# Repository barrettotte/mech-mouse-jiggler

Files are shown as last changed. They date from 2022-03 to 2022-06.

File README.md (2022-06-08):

# mech-mouse-jiggler

A very impractical and stupid mouse jiggler using a crank mechanism, 12V DC motor, and a PWM circuit.

## Purpose

I wanted a basic project with some gears, a mechanical movement, and a DC motor. 
So this was the simplest thing I could think of; Move a mouse back and forth.

The mechanical movement and gears gave me more experience with components/joints in Fusion 360.
I also took the opportunity to learn KiCad and design a PCB for my basic PWM circuit.

## Finished Project

Definitely not perfect and I kept finding flaws. But, it was good enough for the project scope I made.





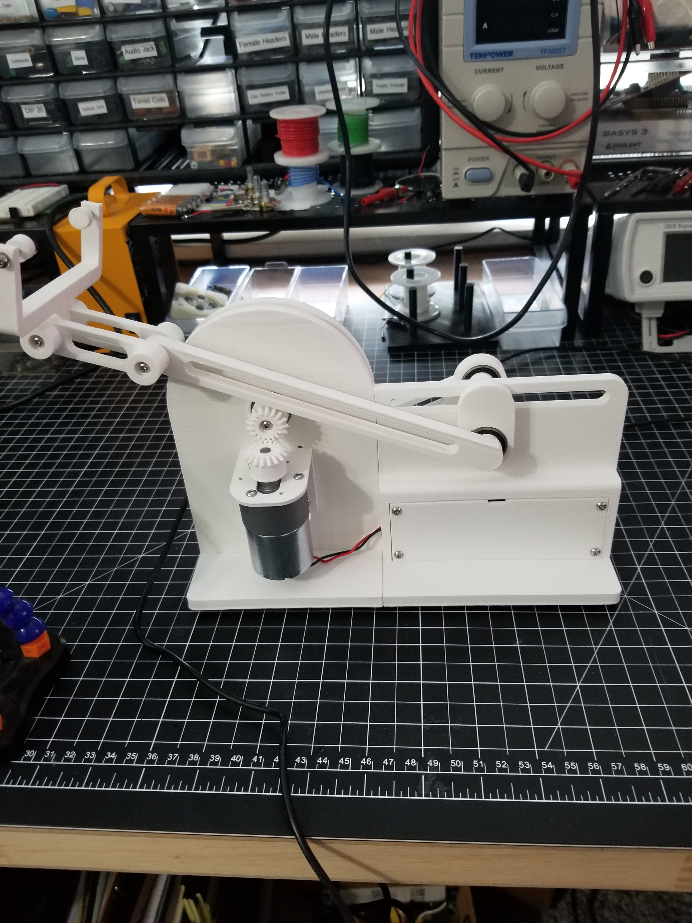
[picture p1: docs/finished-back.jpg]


https://user-images.githubusercontent.com/15623775/172682833-343187b7-290f-4d06-a3b5-5a9f5e372b6b.mp4

https://user-images.githubusercontent.com/15623775/172682868-b304a3e7-49c9-4841-98fb-ab1815b85bfa.mp4

## PWM Circuit

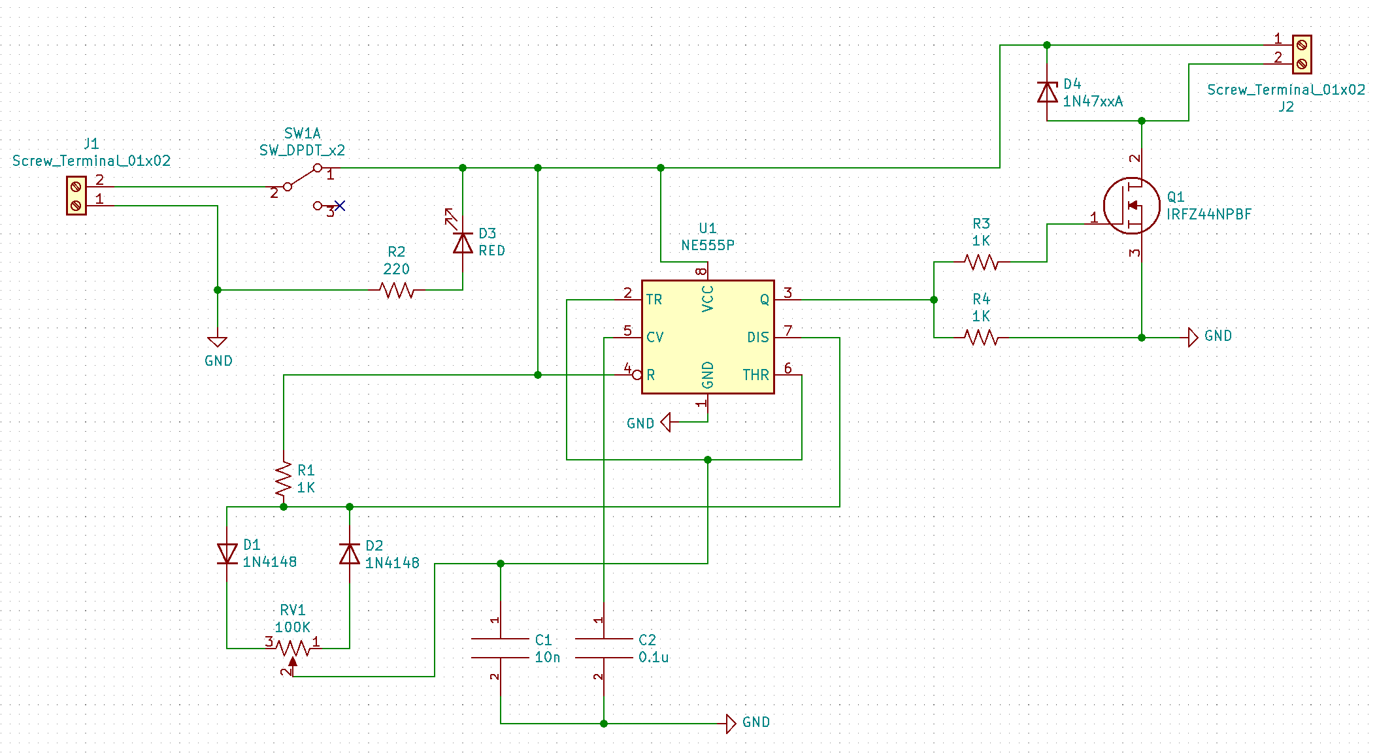
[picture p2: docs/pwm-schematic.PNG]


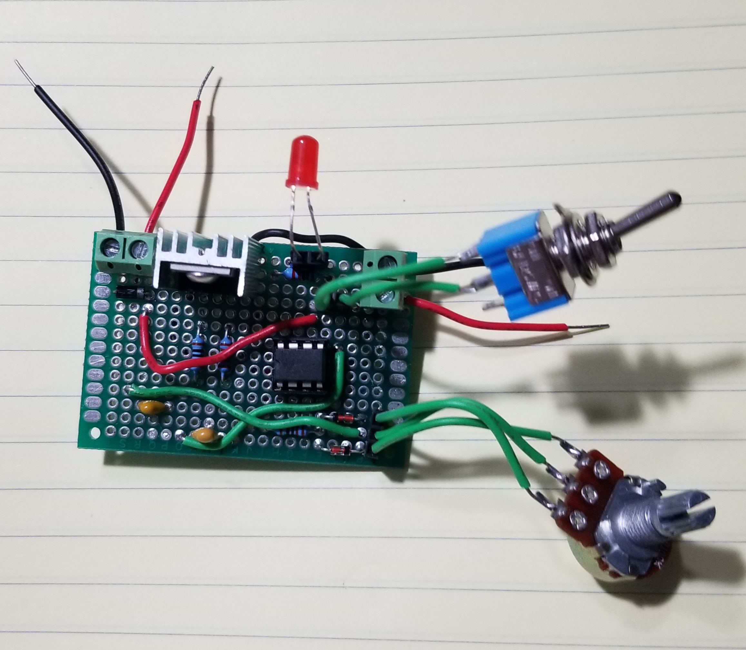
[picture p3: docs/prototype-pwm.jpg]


Crank Test 1 (https://youtube.com/shorts/KTGvGtsnRqs)

Crank Test 2 (https://youtube.com/shorts/8-THsEUhmM4)

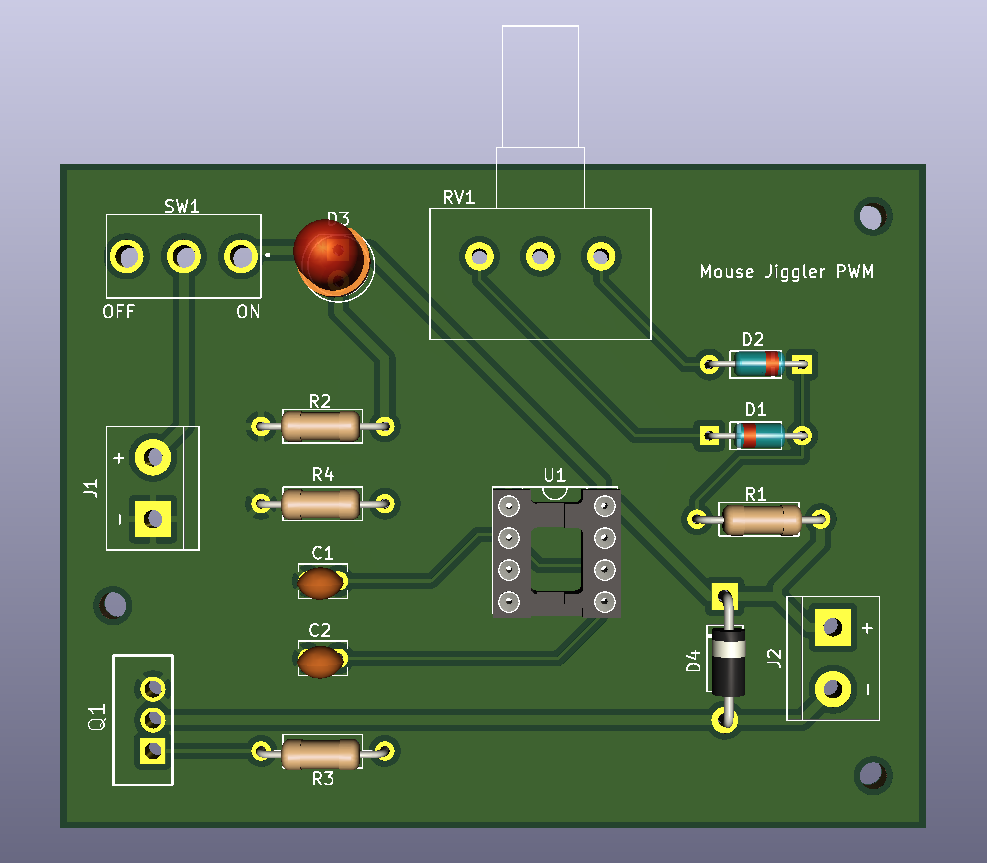
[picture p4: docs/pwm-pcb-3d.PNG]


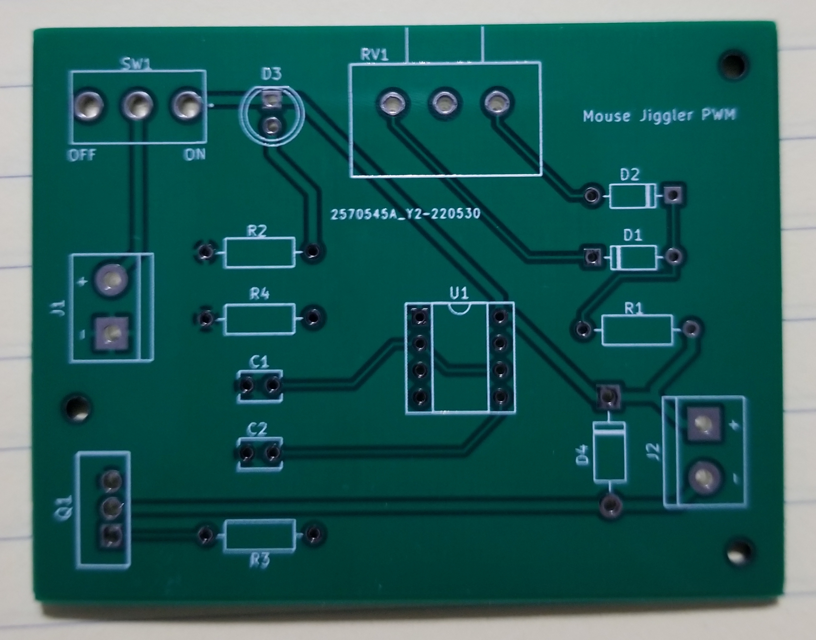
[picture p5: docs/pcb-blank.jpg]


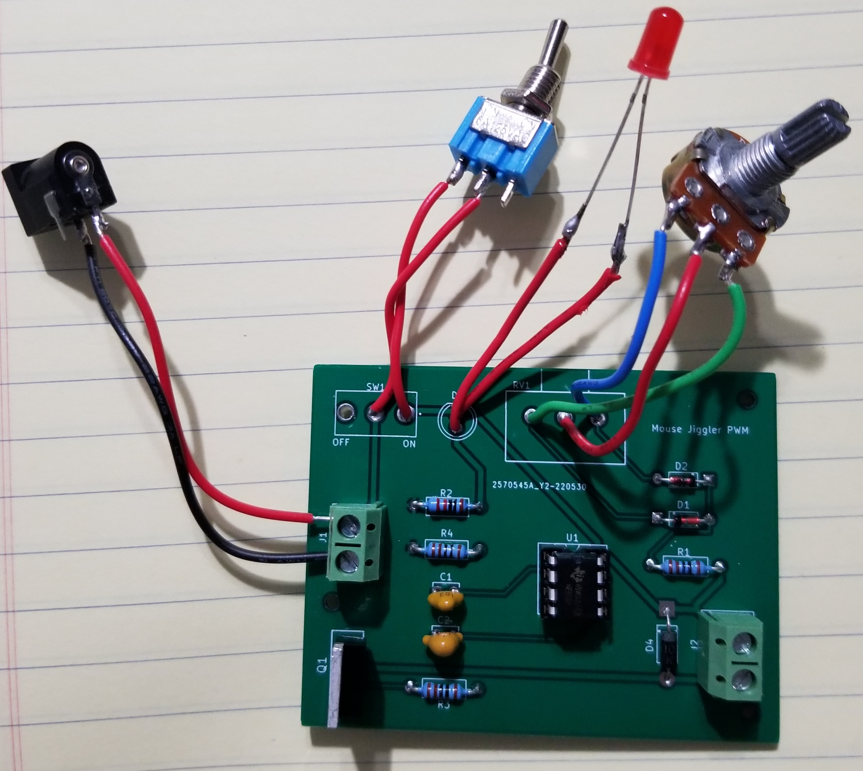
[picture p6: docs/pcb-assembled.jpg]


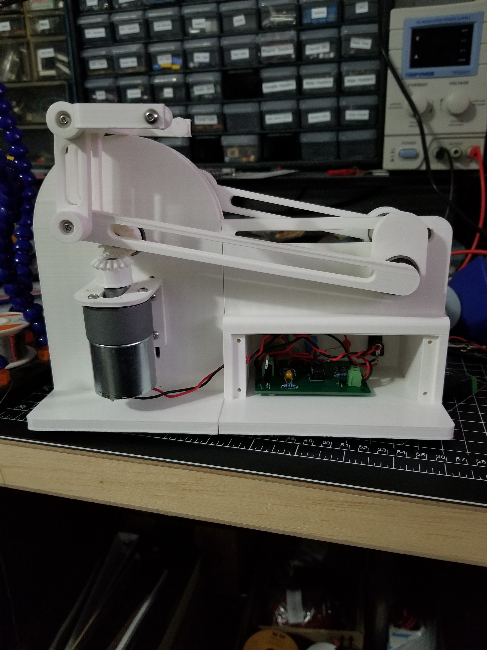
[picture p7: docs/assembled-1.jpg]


## References

- [507 Movements #92](http://507movements.com/mm_092.html)
- [507 Movements #114](http://507movements.com/mm_114.html)
- [KHK Gear Reference](https://khkgears.net/new/gear_knowledge/gear_technical_reference/involute_gear_profile.html)
- [555 Timer PWM circuit](http://www.555-timer-circuits.com/motor-pwm.html)

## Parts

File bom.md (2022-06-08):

# Bill of Materials

## Electronics

| Component Refs | Name | Quantity | Digkey | Link |
| --- | --- | --- | --- | ---- |
| C1 | 10nF Ceramic Capacitor | 1 | 399-5094-ND | https://www.digikey.com/en/products/detail/kemet/C330C102JHR5TA/1465599 |
| C2 | 0.1µF Ceramic Capacitor  | 1 | 399-4329-ND | https://www.digikey.com/en/products/detail/kemet/C322C104K5R5TA/818105 |
| D1,D2 | 1N4148 Diode | 2 | 4167-1N4148-ND | https://www.digikey.com/en/products/detail/diotec-semiconductor/1N4148/16141550 |
| D3 | 5mm Red LED | 1 | 2460-L513SRD-C-ND | https://www.digikey.com/en/products/detail/american-opto-plus-led/L513SRD-C/13556881 |
| D4 | 1N4007T Diode | 1 | 1N4007DICT-ND | https://www.digikey.com/en/products/detail/diodes-incorporated/1N4007-T/607 |
| J1,J2 | 1x2 Terminal Block | 2 | 732-691253910002-ND | https://www.digikey.com/en/products/detail/w%C3%BCrth-elektronik/691253910002/11477907 |
| R1,R3,R4 | 1KΩ Resistor | 3 | CFR25SJT-52-1K-ND | https://www.digikey.com/en/products/detail/yageo/CFR25SJT-52-1K/9098875 |
| R2 | 220Ω Resistor | 1 | CFR25SJT-52-220R-ND  | https://www.digikey.com/en/products/detail/yageo/CFR25SJT-52-220R/9098891 |
| RV1 | 100KΩ Potentiometer | 1 | PDB181-K220K-104B-ND | https://www.digikey.com/en/products/detail/bourns-inc/PDB181-K220K-104B/3780702 | 
| SW1 | Toggle Switch | 1 | 2057-SW-T3-2B-A-A3-S1-ND | https://www.digikey.com/en/products/detail/adam-tech/SW-T3-2B-A-A3-S1/15284416 |
| Q1 | IRFZ44N MOSFET | 1 | IRFZ44NLPBF-ND | https://www.digikey.com/en/products/detail/infineon-technologies/IRFZ44NLPBF/811989 |
| U1 | NE555P IC | 1 | 296-NE555P-ND | https://www.digikey.com/en/products/detail/texas-instruments/NE555P/277057 |
| - | 8 pin DIP socket | 1 | 1175-1486-ND | https://www.digikey.com/en/products/detail/cnc-tech/245-08-1-03/3441579 |
| - | Male barrel jack | 1 | CP-102A-ND | https://www.digikey.com/en/products/detail/cui-devices/PJ-102A/275425 |

## Mechanical

| Name | Quantity | McMaster-Carr | Link |
| --- | --- | --- | ---- |
| 12V DC 550RPM Gear Motor 37mm Shaft | 1 | - | https://www.amazon.com/gp/product/B072R5G5GR |
| 608 Bearing, 8mm shaft | 4 | 5972K91 | https://www.mcmaster.com/5972K91 |
| M3 Hex Button Cap 16mm | 3 | 92095A184 | https://www.mcmaster.com/92095A184 |
| M3 Hex Button Cap 12mm | 11 | 92095A183 | https://www.mcmaster.com/92095A183 |
| M3 Hex Button Cap 6mm | 5 | 92095A179 | https://www.mcmaster.com/92095A179 |
| M3 nut | 4 | 90592A085 | https://www.mcmaster.com/90592A085 |
| Rubber feet 12mm | 6 | - | https://www.amazon.com/gp/product/B07PXNTT7K |

## 3D Printed

Creality Ender-3 Pro - 0.4mm nozzle, 0.2mm layer height, 20% infill

| Name | Quantity | Model |
| --- | --- | ----- |
| Arm | 1 | [cad/arm.3mf](cad/arm.3mf) |
| Arm connector | 2 | [cad/arm_connector.3mf](cad/arm_connector.3mf) |
| Base | 1 | [cad/base.3mf](cad/base.3mf) |
| Base electonics | 1 | [cad/base_electronics.3mf](cad/base_electronics.3mf) |
| Bearing cap | 3 | [cad/bearing_cap.3mf](cad/bearing_cap.3mf) |
| Bevel gear motor  | 1 | [cad/bevel_gear_motor.3mf](cad/bevel_gear_motor.3mf) |
| Bevel gear wheel  | 1 | [cad/bevel_gear_wheel.3mf](cad/bevel_gear_wheel.3mf) |
| Coupler | 1 | [cad/coupler.3mf](cad/coupler.3mf) |
| Electronics Cover | 1 | [cad/electronics_cover.3mf](cad/electronics_cover.3mf) |
| Load arm | 1 | [cad/load_arm.3mf](cad/load_arm.3mf) |
| Motor mount | 1 | [cad/motor_mount.3mf](cad/motor_mount.3mf) |
| Mouse clamp | 1 | [cad/mouse_clamp.3mf](cad/mouse_clamp.3mf) |
| Mouse clamp cap | 2 | [cad/mouse_clamp_cap.3mf](cad/mouse_clamp_cap.3mf) |
| Wheel spacer | 3 | [cad/wheel_spacer.3mf](cad/wheel_spacer.3mf) |
| Wheel | 1 | [cad/wheel.3mf](cad/wheel.3mf) |

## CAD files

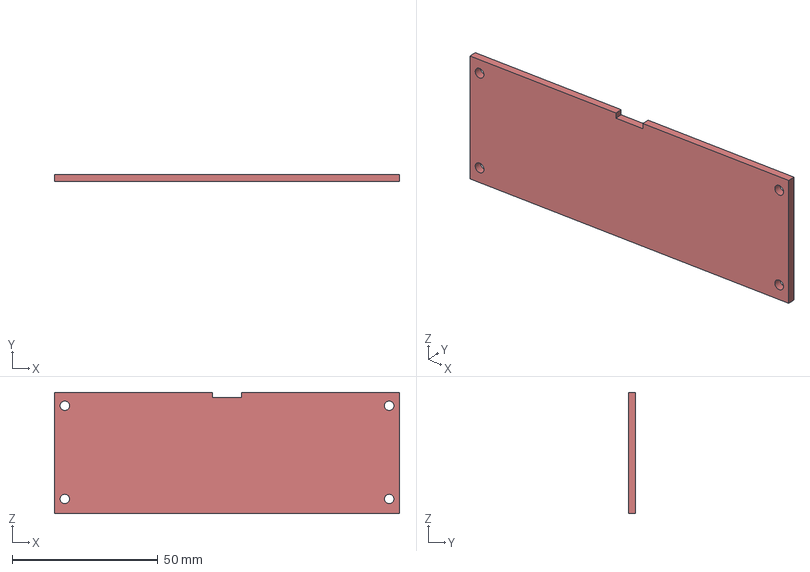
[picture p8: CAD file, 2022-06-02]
cad/electronics-cover.3mf
118.5 x 2.50 x 41.5 mm

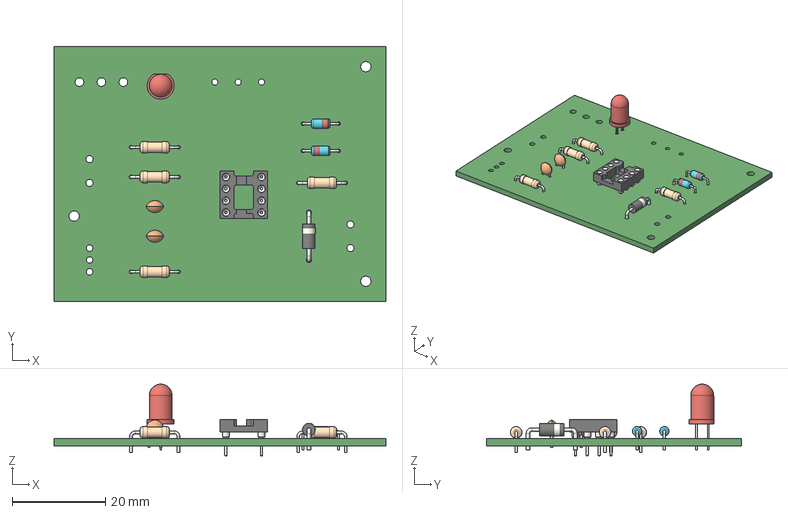
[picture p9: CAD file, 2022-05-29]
eda/mouse-jiggler-pwm.step
71.1 x 54.6 x 15.4 mm

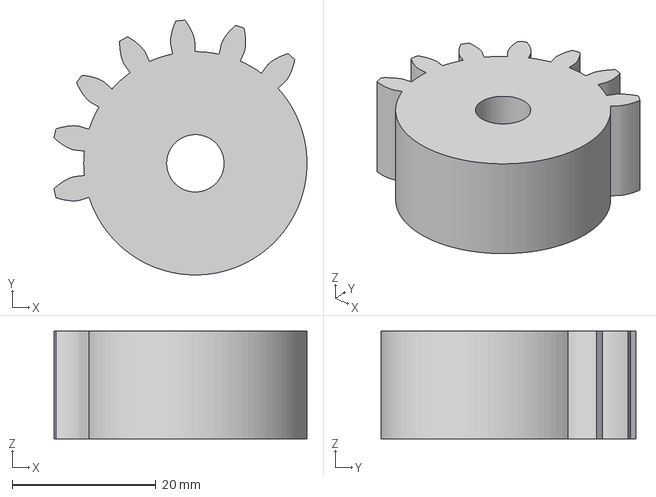
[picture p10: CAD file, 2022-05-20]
test/movement-114/mutilated-spur-gear-15-7.3mf
35.2 x 35.5 x 15.0 mm

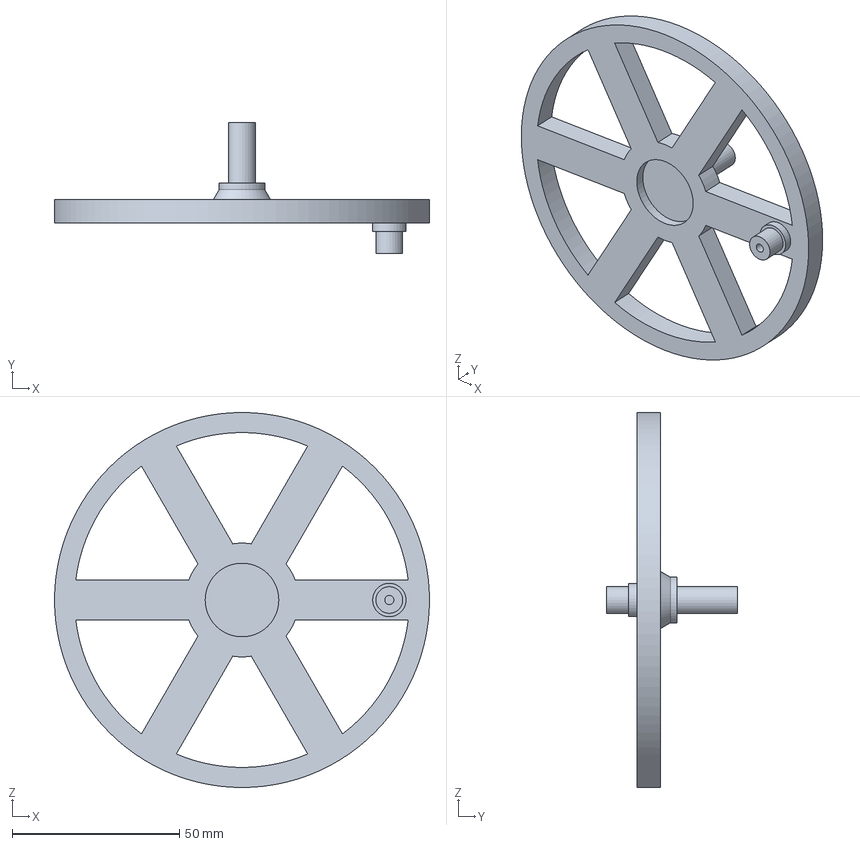
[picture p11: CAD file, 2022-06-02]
cad/wheel.3mf
112.0 x 39.0 x 112.0 mm

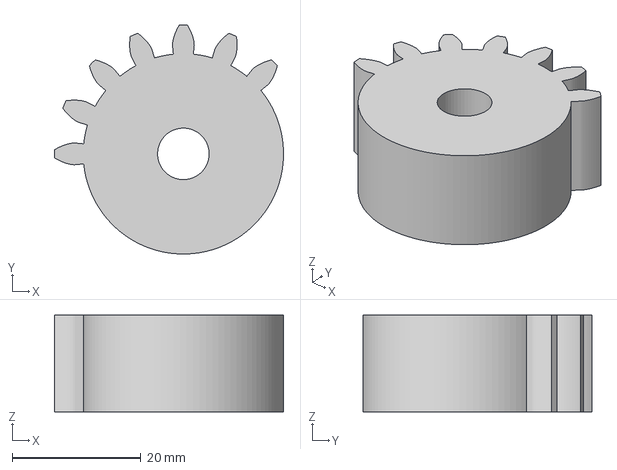
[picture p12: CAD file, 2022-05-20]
test/movement-114/mutilated-spur-gear-16-7.3mf
35.5 x 35.5 x 15.0 mm

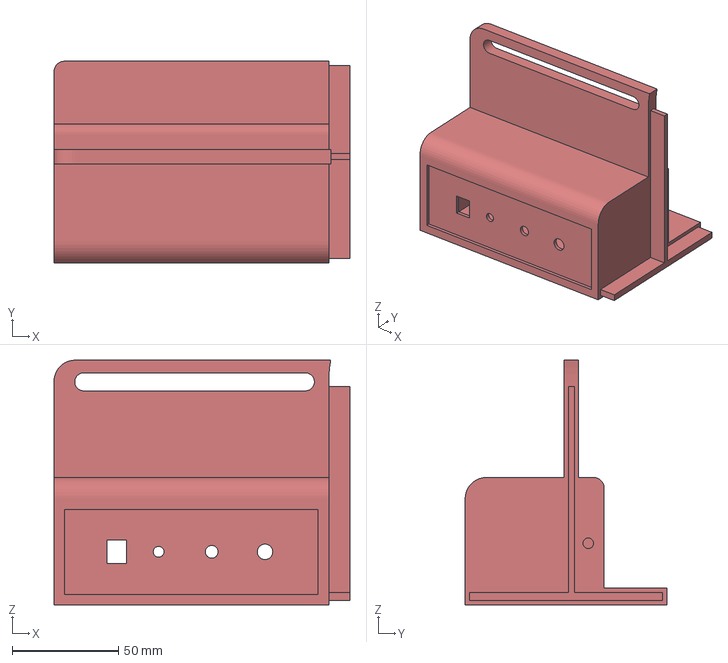
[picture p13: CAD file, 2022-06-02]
cad/base-electronics.3mf
139.4 x 95.0 x 115.2 mm

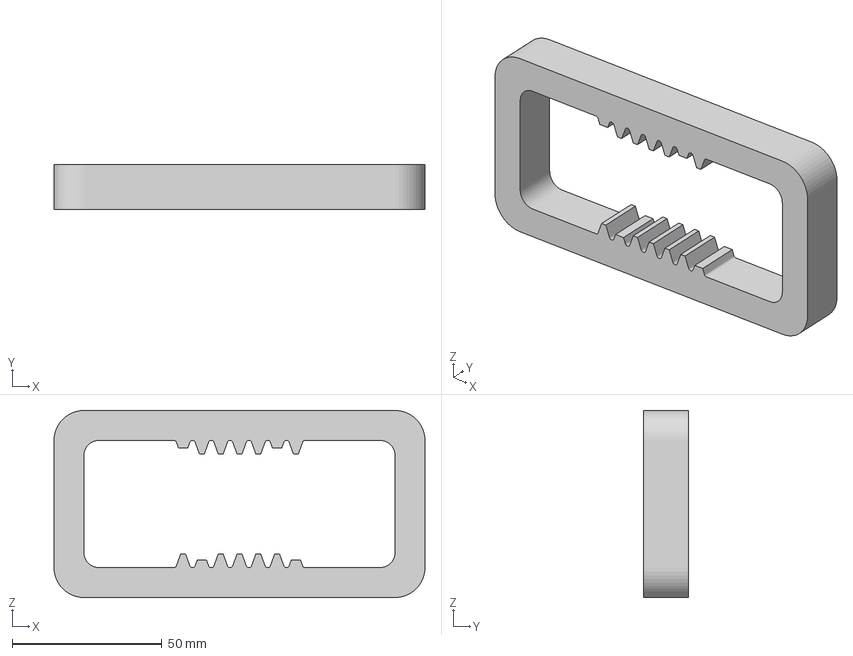
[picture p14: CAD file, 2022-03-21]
test/movement-114/rack.3mf
124.0 x 15.0 x 62.5 mm

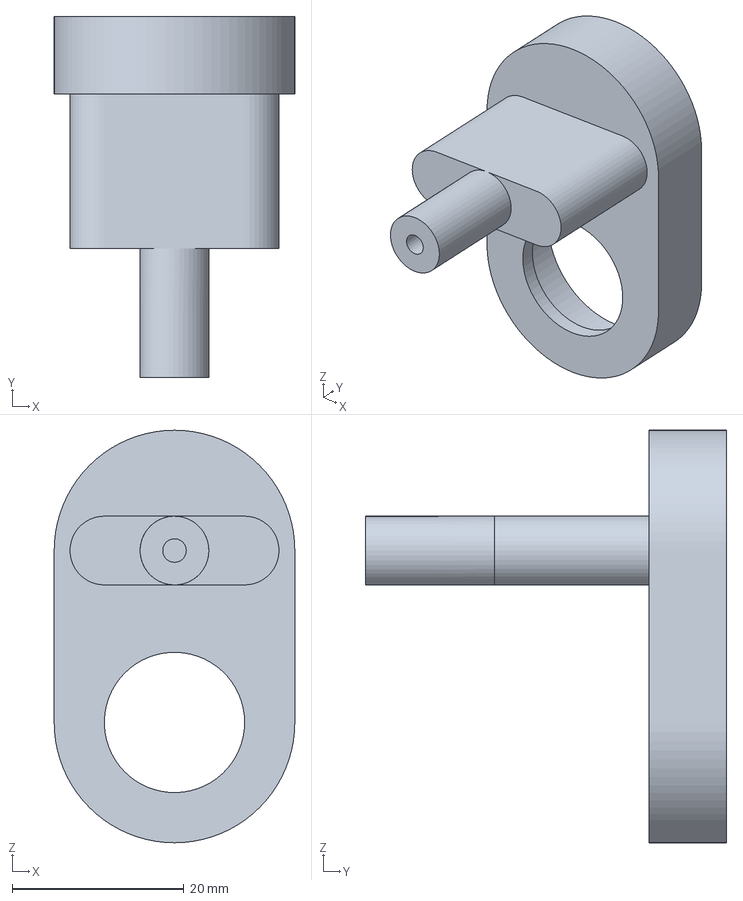
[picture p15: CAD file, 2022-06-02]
cad/coupler.3mf
28.0 x 42.0 x 48.0 mm

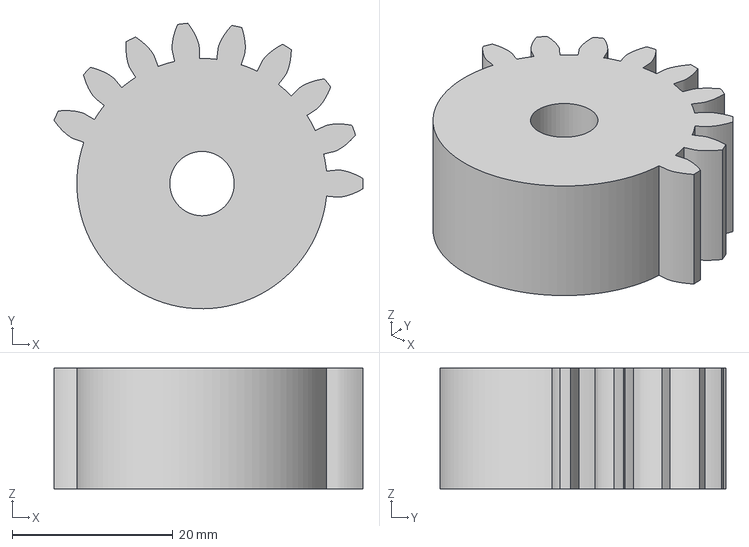
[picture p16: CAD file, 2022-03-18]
test/movement-114/spur-gear-9-155.3mf
38.4 x 35.5 x 15.0 mm

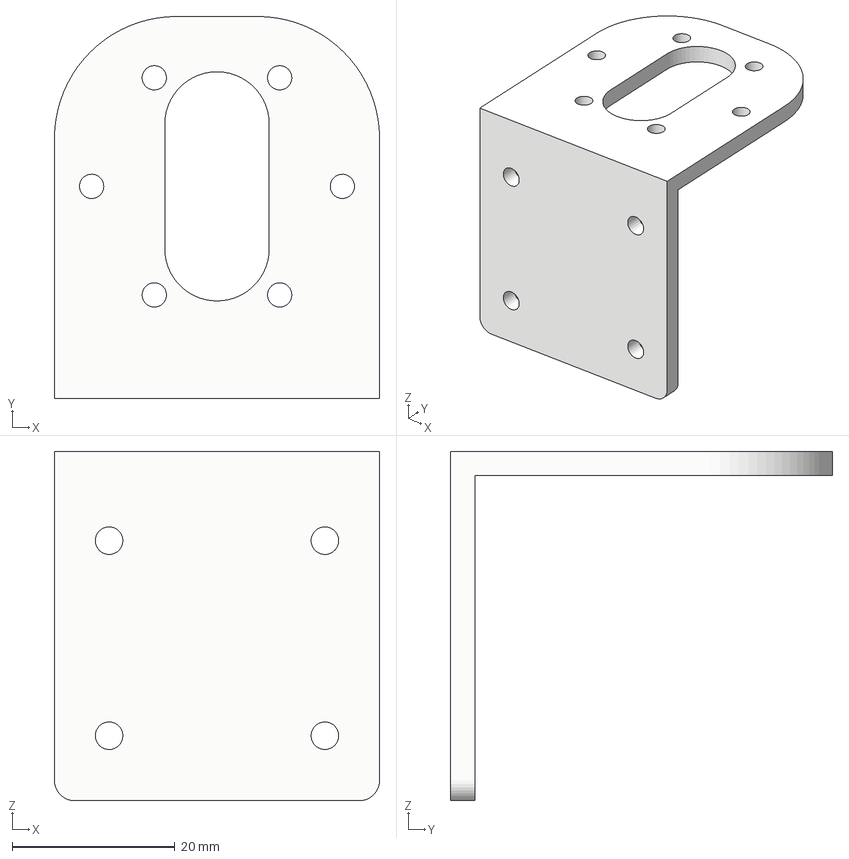
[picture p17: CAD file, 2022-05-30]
cad/motor-mount.3mf
40.0 x 47.0 x 43.0 mm

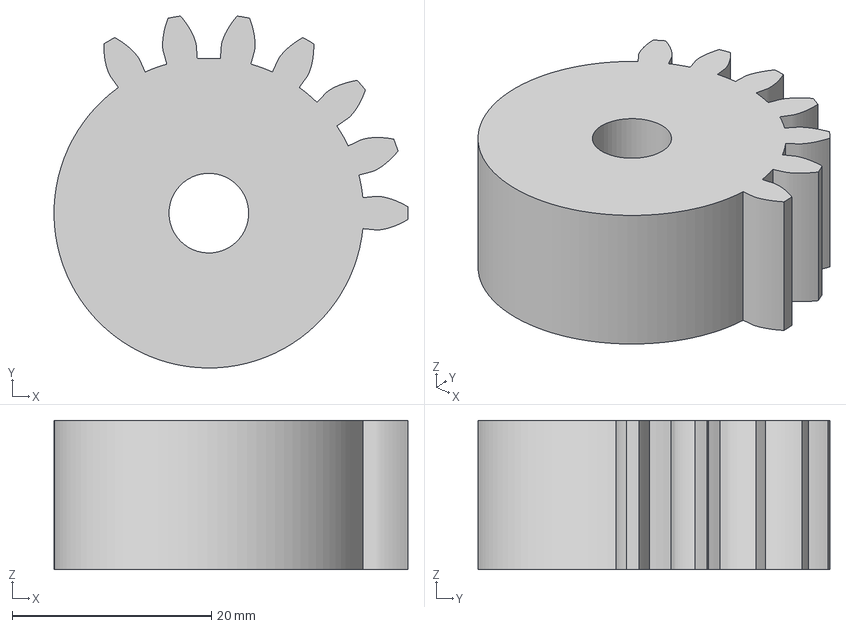
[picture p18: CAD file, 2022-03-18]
test/movement-114/spur-gear-7-120.3mf
35.5 x 35.3 x 15.0 mm

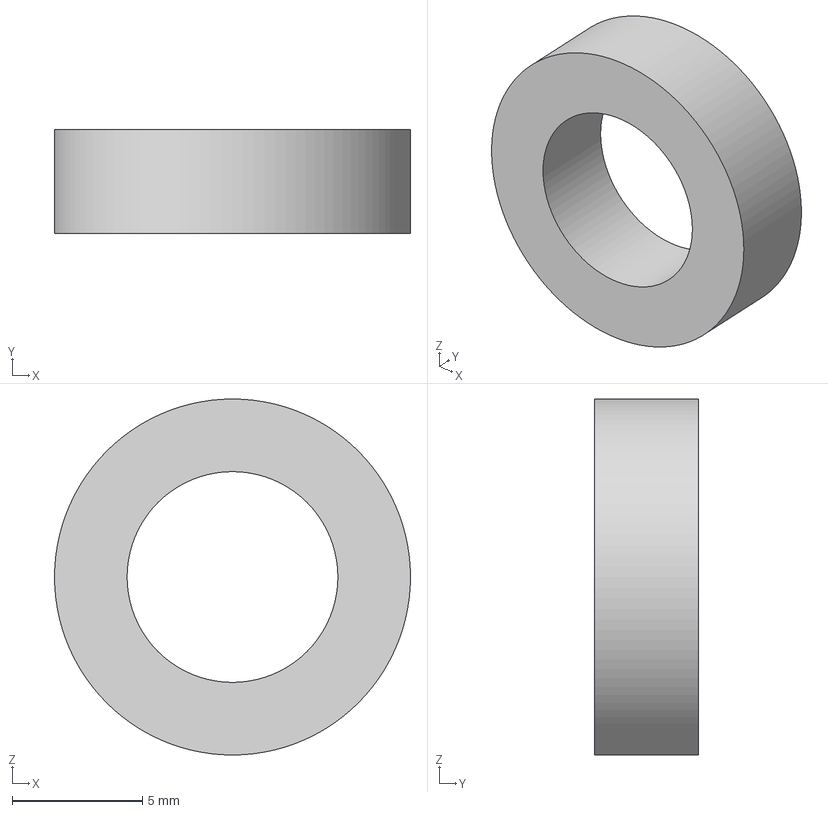
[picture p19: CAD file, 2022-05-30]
cad/wheel-spacer.3mf
13.7 x 4.00 x 13.7 mm

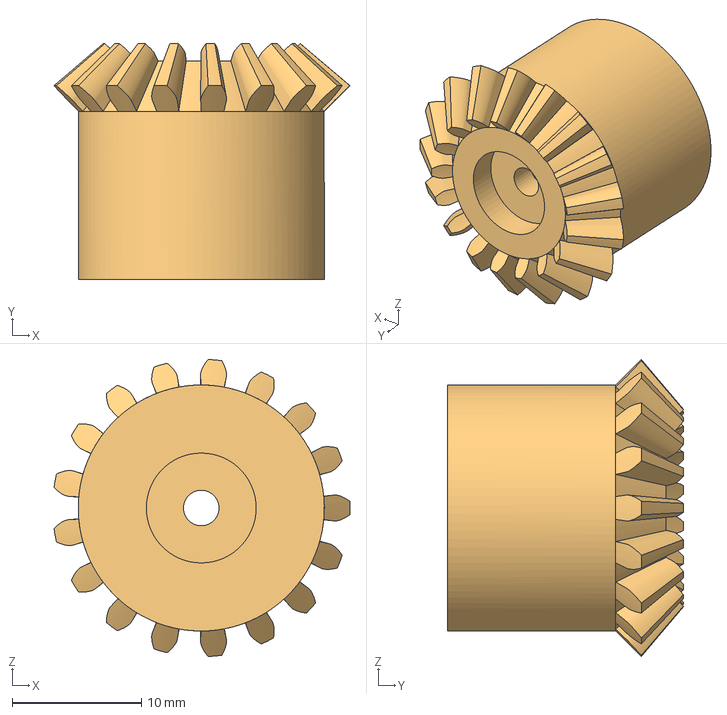
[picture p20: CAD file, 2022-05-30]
cad/bevel-gear-wheel.3mf
22.9 x 18.2 x 23.0 mm

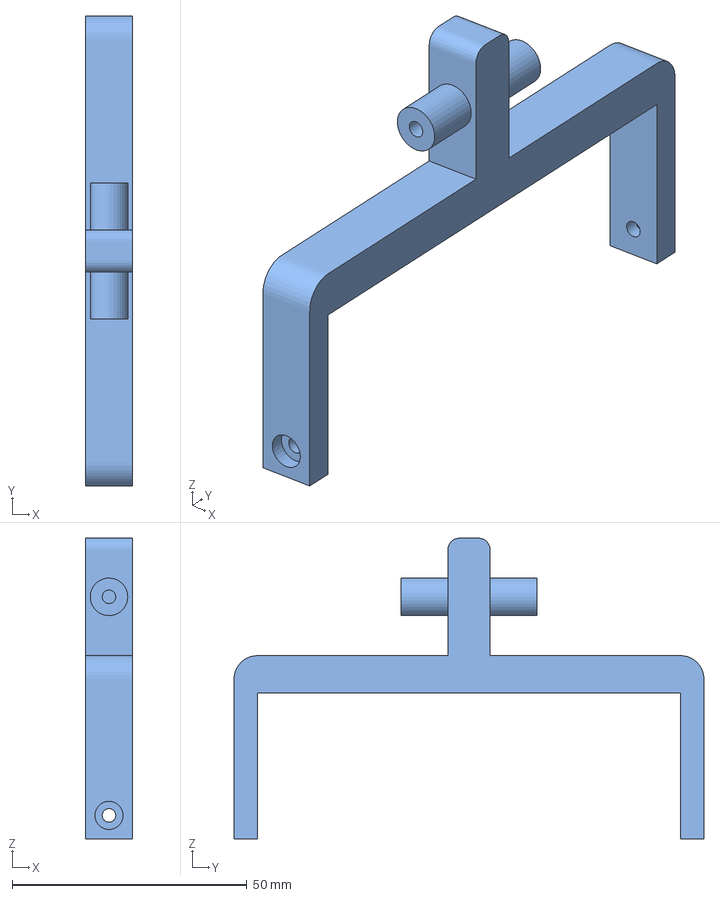
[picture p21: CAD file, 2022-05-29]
cad/mouse-clamp.3mf
10.0 x 100.0 x 64.0 mm

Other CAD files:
test/movement-114/spur-gear-7-135.3mf
cad/base.3mf
cad/mouse-clamp-cap.3mf
cad/load-arm.3mf
cad/arm-connector.3mf
cad/arm.3mf
cad/bearing_cap.3mf
cad/bevel-gear-motor.3mf
test/movement-114/movement-114 v32.f3d
test/movement-92/movement-92 v4.f3d

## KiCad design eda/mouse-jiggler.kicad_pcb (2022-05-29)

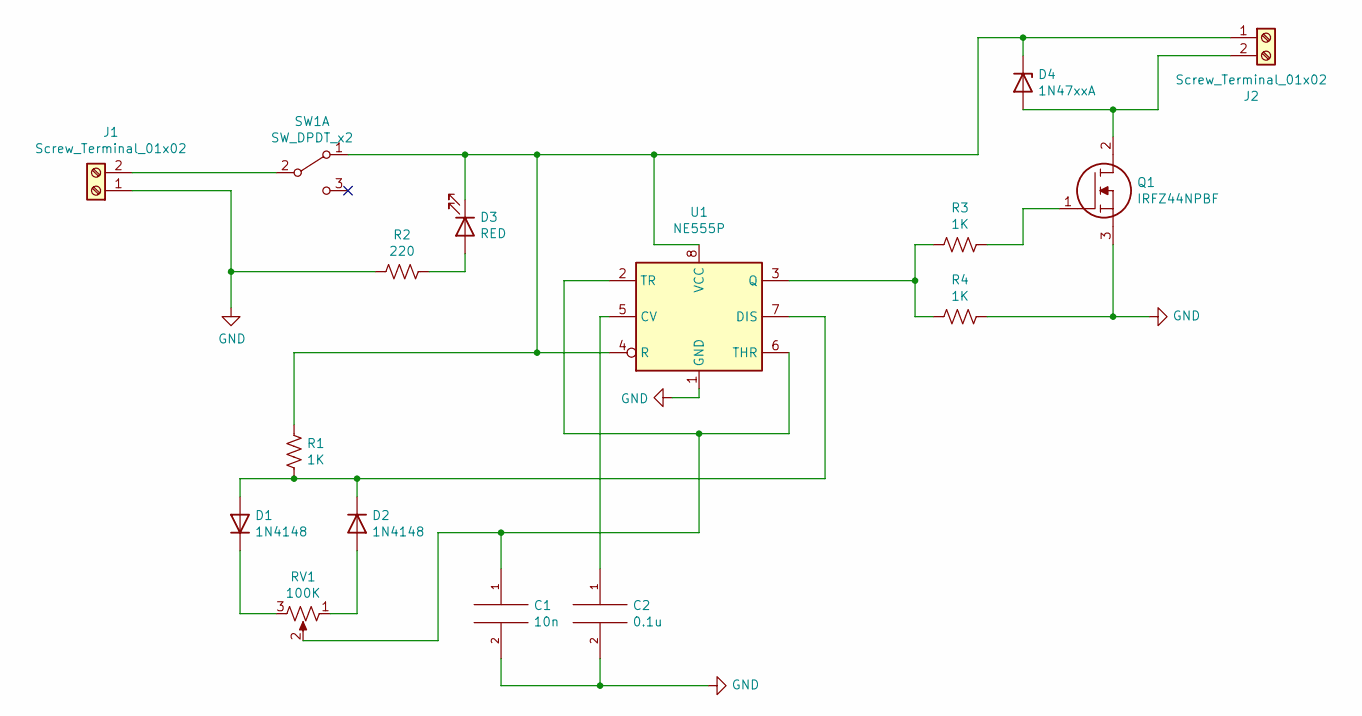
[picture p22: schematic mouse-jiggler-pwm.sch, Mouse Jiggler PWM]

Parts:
C1: 10n; C_Disc_D3.8mm_W2.6mm_P2.50mm
C2: 0.1u; C_Disc_D3.8mm_W2.6mm_P2.50mm
D1, D2: 1N4148; D_DO-35_SOD27_P7.62mm_Horizontal
D3: RED; LED_D5.0mm
D4: 1N47xxA; D_DO-41_SOD81_P10.16mm_Horizontal
J1, J2: Screw_Terminal_01x02; TerminalBlock_bornier-2_P5.08mm
Q1: IRFZ44NPBF; TO254P483X1016X1994-3P; Mouser Part Number 942-IRFZ44NPBF
R1, R3, R4: 1K; R_Axial_DIN0207_L6.3mm_D2.5mm_P10.16mm_Horizontal
R2: 220; R_Axial_DIN0207_L6.3mm_D2.5mm_P10.16mm_Horizontal
RV1: 100K; Potentiometer_Alps_RK163_Single_Horizontal
SW1: SW_DPDT_x2; 100SP1T1B4M2QE
U1: NE555P; DIP-8_W7.62mm_Socket

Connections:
GND: C1.2, C2.2, J1.1, Q1.3, R2.2, R4.1, U1.1 (GND)
unnamed: C1.1, RV1.2, U1.2 (TR), U1.6 (THR)
unnamed: C2.1, U1.5 (CV)
unnamed: D1.1 (K), RV1.3
unnamed: D1.2 (A), D2.1 (K), R1.2, U1.7 (DIS)
unnamed: D2.2 (A), RV1.1
unnamed: D3.1 (K), D4.1 (K), J2.1, R1.1, SW1.1 (A), U1.4 (R), U1.8 (VCC)
unnamed: D3.2 (A), R2.1
unnamed: D4.2 (A), J2.2, Q1.2
unnamed: J1.2, SW1.2 (B)
unnamed: Q1.1, R3.1
unnamed: R3.2, R4.2, U1.3 (Q)

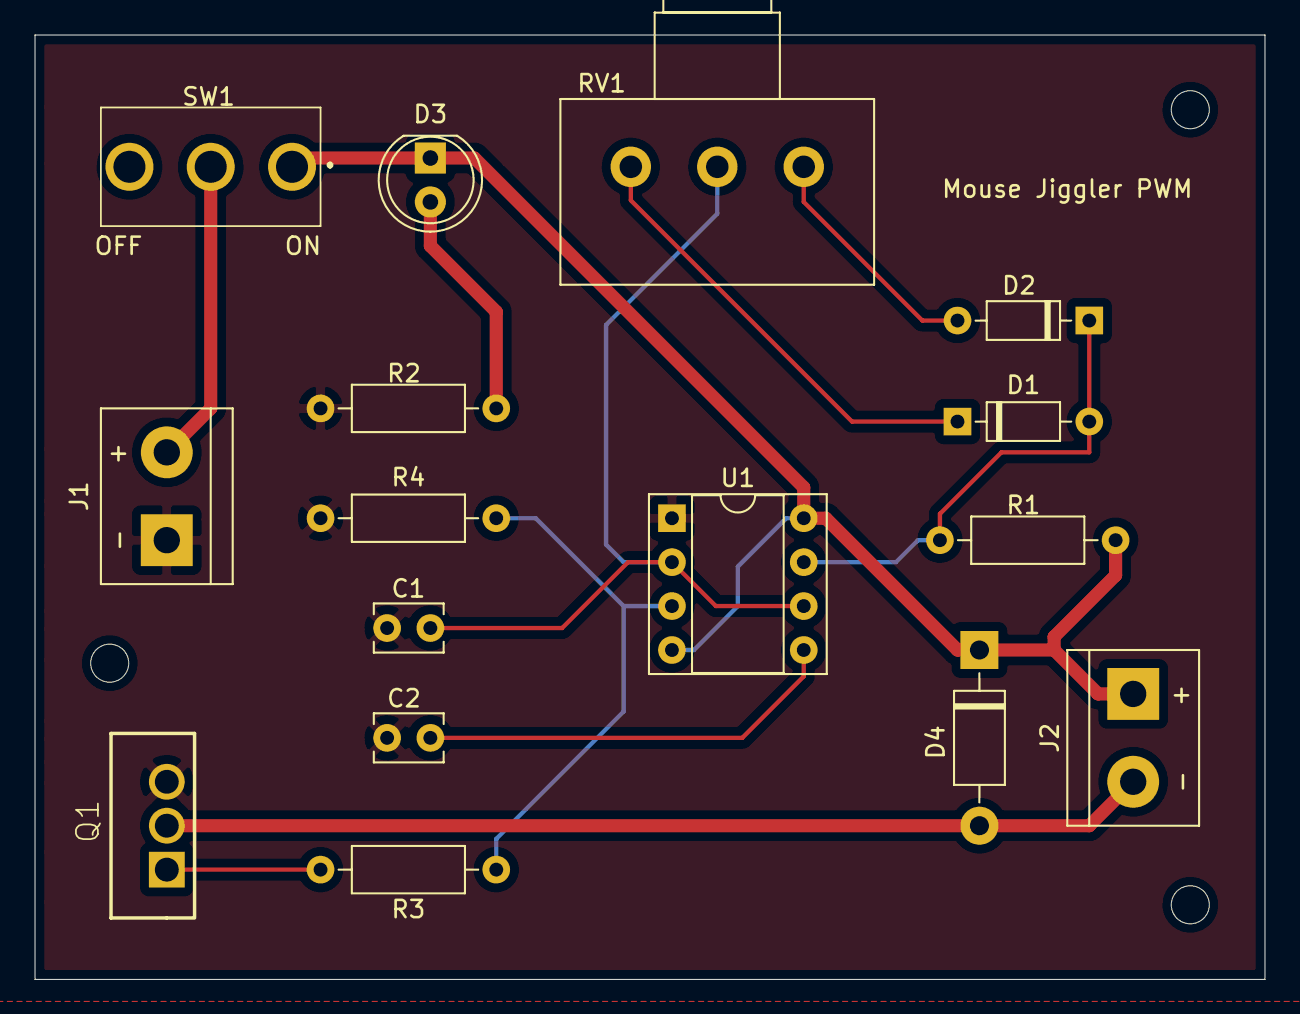
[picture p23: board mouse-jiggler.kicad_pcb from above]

Board: 2 copper layers, 71.1 x 54.6 mm, 16 parts (0 on the bottom side), 12 nets.

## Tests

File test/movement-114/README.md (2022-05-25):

# Movement 114

Uniform circular motion into reciprocating rectilinear motion, by means of mutilated pinion, which drives alternately the top and bottom rack.

http://507movements.com/mm_114.html

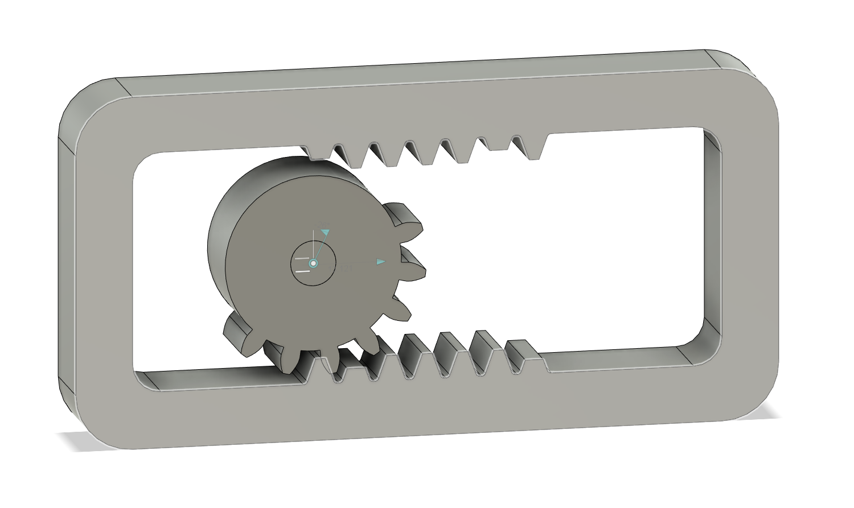
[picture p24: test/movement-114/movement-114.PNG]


- rack
  - 9 teeth top/bottom
  - backlash = 0.15mm
  - thickness = 15mm
- spur gear
  - 135 deg radial, 7 teeth
  - module = 2mm
  - backlash = 0.15mm
  - gear thickness = 15mm

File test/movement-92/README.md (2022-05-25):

# Movement 92

Ordinary crank motion.

http://507movements.com/mm_092.html

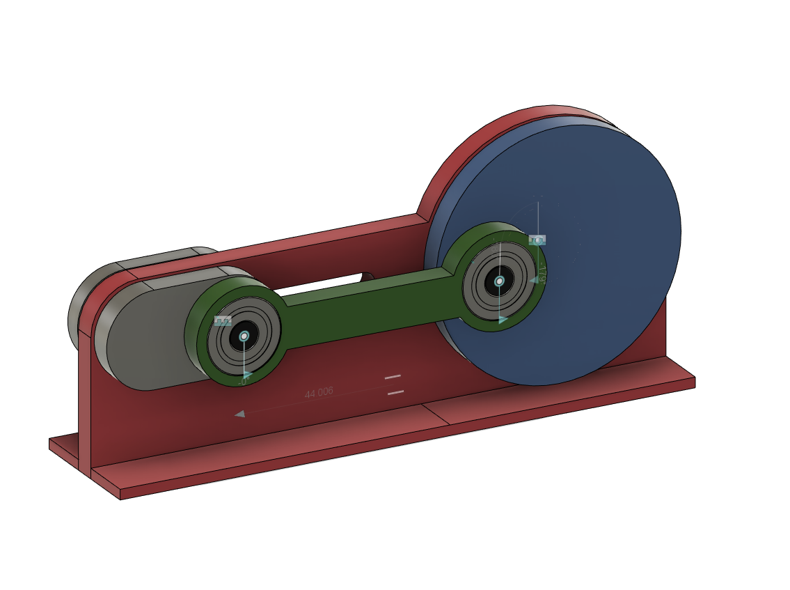
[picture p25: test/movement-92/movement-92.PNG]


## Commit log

2022-03-17 test 114 movement
    [rack.3mf, spur-gear.3mf]
2022-03-18 movement 114 test
    [rack.3mf, spur-gear-7-120.3mf, spur-gear-7-135.3mf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]
2022-03-21 114 test
    [mutilated-spur-gear-7.3mf, rack.3mf]
2022-05-20 movement 92 test
    [movement-114 v32.f3d, movement-92 v4.f3d, mutilated-spur-gear-15-7.3mf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]
2022-05-25 base design
    [arm.3mf, wheel.3mf]
2022-05-27 basic components cad
    [arm-connector.3mf, arm.3mf, bearing_cap.3mf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]
2022-05-27 basic kicad schematic
    [mouse-jiggler-pwm.sch, mouse-jiggler.kicad_pcb]
2022-05-29 fix mouse clamp
    [base-electronics.3mf, base.3mf, mouse-clamp-cap.3mf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]
2022-05-29 pcb footprint layout
    [mouse-jiggler-pwm.sch, mouse-jiggler.kicad_pcb]
2022-05-29 fix toggle switch footprint and generate gerber
    [mouse-jiggler-B_Cu.gbl, mouse-jiggler-B_Mask.gbs, mouse-jiggler-B_Paste.gbp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]
2022-05-29 add PWM circuit CAD to fusion 360 project
    [base-electronics.3mf, mouse-jiggler-pwm.step]
2022-05-30 fix Gerber zip
2022-05-30 tweak gear bevel gear, add wheel spacer, add motor mount
    [bevel-gear-wheel.3mf, motor-mount.3mf, wheel-spacer.3mf]
2022-05-30 double thickness of motor mount
    [motor-mount.3mf]
2022-06-02 tweak wheel and coupler dimensions
    [base-electronics.3mf, coupler.3mf, wheel.3mf]
2022-06-02 added electronics base cover
    [electronics-cover.3mf]
2022-06-02 tweak and add pry hole to electronics cover
    [electronics-cover.3mf]
2022-06-07 add mechanical bom

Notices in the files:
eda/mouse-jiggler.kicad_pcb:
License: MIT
